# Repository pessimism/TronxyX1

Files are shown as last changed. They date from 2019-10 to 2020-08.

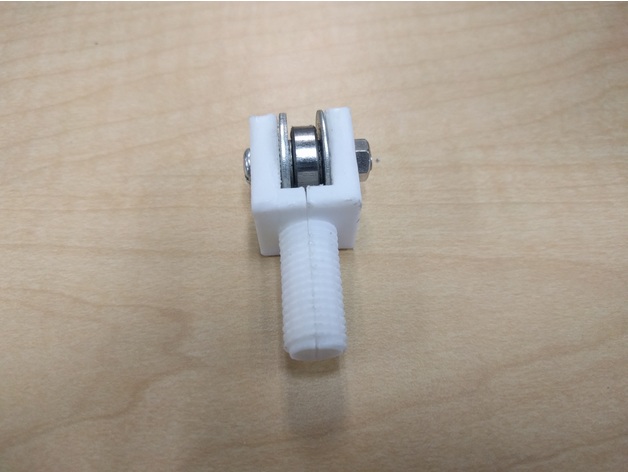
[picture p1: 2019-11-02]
Models/Parts/3d_printer_belt_tensioner/images/830ebf25c9036d7032c9400a6b96da95_preview_featured.jpg

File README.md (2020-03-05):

# TronxyX1

## Introduction

The [Tronxy X1](http://www.tronxy.com/x-series/tronxy-x1.html) is a budget cantilever design 3D printer by Tronxy.  I purchased this as my entry into the world of 3D printing.  

This repository contains documentation and resources I have collected while experimenting with this printer.

## Purchasing

All purchasing information here is focused on purchasing from Canada in Canadian Dollars (CAD).

I purchased my Tronxy X1 at [GearBest](https://www.gearbest.com/3d-printers-3d-printer-kits/pp_494192.html).  At the time of purchase, the kit was on flash sale for $133.  I was not given an option to choose shipping for this deal.  It was shipped by DHL and time from order to arrival was one week including a weekend.  There were some surprise customs fees from DHL bringing total cost to $159 to my door.  To their credit, DHL made payment of customs fees a painless online process and sent SMS status messages about the shipment and the need to pay fees.  

My first filament purchase was the [Sunlu PLA+](http://www.sunlugw.com/pd.jsp?id=52#_pp=151_1343) from [Amazon Canada](https://www.amazon.ca/gp/product/B07FXJ6PKQ/ref=ppx_yo_dt_b_asin_title_o04_s00?ie=UTF8&psc=1).  Cost for the 1KG spool was $20.39 on sale plus taxes totalling $23.04 (I have a Prime membership so did not pay extra for shipping).  The filament appears to be of good quality so far and I have not yet had any clogging or other issues caused by filament quality.

[CCTREE PLA](https://www.amazon.ca/CCTREE-1-75mm-PLA-Printer-Filament/dp/B07737W8Y9) So far seems to print at a lower temperature with fewer stringing/blobbing issues than the Sunlu.

I purchased this [ten pack of roller wheels](https://www.amazon.ca/gp/product/B07CWM3GCM/ref=ppx_yo_dt_b_asin_title_o03_s00?ie=UTF8&psc=1) at a shipped cost of $1.58 each to replace one wheel shipped with the unit that was scratched causing the x-axis to catch on the rail at a certain point.  The new wheel worked but these appear to be of poor quality, do not spin effortlessly by hand and have slight surface imperfections in the plastic.  I will search for higher quality rollers later as an upgrade option.

## Folder Structure

Documentation - The factory documentation shipped with the printer

Drivers - The USB to serial interface driver required to control the printer by computer

Models - Model files for the factory demo part, useful calibration items and upgrade parts specific to the printer

Profiles - Printer and Filament configuration profiles I have built and found to work well with my particular setup.

Marlin 2.0 Config - Configuration files to build Marlin 2.0 firmware for the printer

## Bed Adhesion

I had difficulty with adhesion with the bare Garolite build plate and Sunlu PLA+.  I added a layer of inexpensive 3M green painter's tape locally purchased and had much better results.

After printing and removing several items I had adhesion issues again which were improved by wiping down the tape surface with alcohol, finger oils can make the difference between adhesion and failure.

After more printing I've abandoned the tape for now and lightly sanded the Garolite with sandpaper, cleaned with alcohol and use a layer of cheap glue stick that I wash off and reapply every few prints.  I find this faster and simpler than dealing with the tape, which I have found in some instances can actually be lifted off the Garolite by a warping print.

## Firmware Calibration
I found that even after belt tensioning to the best of my ability with the provided hardware, I had to very slightly increase the X steps/mm to get true squares/circles.  I attribute this to differences in belt tension between axes

I found my extruder was underextruding and steps/mmm needed to be increased by almost 10%.  Never assume factory calibration is correct.  This can also change from one filament to the other.  I did the adjustment using [this guide](https://all3dp.com/2/extruder-calibration-6-easy-steps-2/)

## Extruder Issues
While trying to eliminate stringing and blobbing on prints I found that the bowden tube was not fully inserted into either coupler.  The end going into the hot end was also not cut flat, so I re-trimmed the end. Trimming and re-seating the tube noticeably improved print quality.

## Marlin 2.0
I opted to upgrade the printer to Marlin 2.0 from the stock Repetier 0.91 firmware.  This gave me thermal runaway protection, a serious omission from the printer.  I was also able to add several features from much more expensive units such as print pausing and resume from power failure.  This process requires several parts to be purchased as the stock Melzi board does not ship with a bootloader installed so it can't be flashed by USB.  The way I completed the process requires:

[An Arduino UNO or compatible board](https://www.amazon.ca/gp/product/B01MTMDT29/ref=ppx_yo_dt_b_asin_title_o04_s00?ie=UTF8&psc=1) ~$15

[Female to Female AND Female to Male Dupont Jumper Wires](https://www.amazon.ca/gp/product/B01EV70C78/ref=ppx_yo_dt_b_asin_title_o02_s00?ie=UTF8&psc=1) ~$12

A computer with the [Arduino IDE](https://www.arduino.cc/en/Main/Software) installed

A copy of the [Marlin 2.0 Source Code](http://marlinfw.org/meta/download/)

I will not detail all steps here as there are several good guides available online to outline the process.  I found [this one](https://www.instructables.com/id/Flashing-a-Bootloader-to-the-CR-10/) to be the most accurate.  In a nutshell you must

+ Program the UNO device via USB to act as a flashing tool 
+ Wire the UNO device to the Melzi board using six jumper wires
+ Flash a bootloader to the Melzi board via PC USB -> UNO -> Melzi connection
+ Disconnect UNO board
+ Build Marlin 2.0 using the correct Configuration.h file and any further adjustments to the Configuration_adv.h file
+ Flash Marlin to the Melzi board via PC USB

I had to make a few adjustments to the stock example Configuration and Configuration_adv files for the Tronxy X1:

+ The bed offsets were incorrect so prints were not centered in the print area
+ The thermal runaway protection was too aggressive for my room temperature and heater calibration and would error before heating was complete.  I relaxed the values as described in the documentation
+ I added my PID heater calibration values to replace the firmware defaults and made sure PID temperature control was enabled.  Further information [here](https://reprap.org/wiki/PID_Tuning)
+ I've noticed some inconsistencies in the keys required to activate menu items.  Some use left/right, some use up to confirm.  Have not resolved that yet, but all functions do work.

## Belt idler upgrade to tensioners
I purchased these [2020 extrusion compatible belt tensioners](https://www.aliexpress.com/item/4000056015276.html?spm=a2g0s.9042311.0.0.2c824c4djNLGq6) ~$15 to replace the stock single sided acrylic brackets and smoothg idler bearings.  This was the single largest upgrade in print quality I have done.  They are far better quality than the stock hardware, have toothed idlers to better fit the belt, and made a large improvement in the printer's ability to make accurate circles.  This was noticable right away in the stock demo pillar file included with the printer.  The drawback is a loss of 25mm of bed area due to the Y tensioner stopping the bed wheel from reaching the end of the extrusion.

## Part Cooling Fan
I printed [this](https://www.thingiverse.com/thing:2699842) and added a 5015 fan using spare mounting nuts and screws included with the printer.  There is an open fan header on the Melzi board for this purpose.  To get proper alignment I had to rotate the heat block slightly and tweak the fan mount/shroud a little.  I have found the fan helps to prevent distortion and stringing on small posts, but it also causes the base of parts to curl up off the bed, so it is only useful in specific circumstances.

## Fan Upgrades
I upgraded the hotend fan to [this](https://www.amazon.ca/gp/product/B009NQLT0M/ref=ppx_yo_dt_b_asin_title_o00_s00?ie=UTF8&psc=1) Noctua NF-A4x10 FLX fan for a huge decrease in operating noise.  The high pitched tone from the stock fan is completely gone and I have observed no cooling issues from the lower RPM fan

I am planning to upgrade the generic 5015 fan to [this](https://www.digikey.ca/product-detail/en/sunon-fans/MF50151VX-B00U-A99/259-1829-ND/7691033) Sunon MF50151VX-B00U-A99 fan in hopes to reduce operating noise further

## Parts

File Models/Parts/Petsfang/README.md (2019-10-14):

# Models

In this directory are a collection of models for testing, calibration and improvements for the printer.  Thank you to all of the great creators on thingiverse for sharing their work with the world.

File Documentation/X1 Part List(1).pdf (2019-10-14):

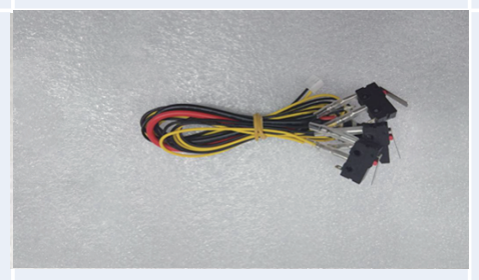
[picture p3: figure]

No. | Picture | Details | Quantity | Check | No. | Picture | Details | Quantity | Check
1-1 | | Limit switch | 3 | | 1-2 | | DC power jack | 1

# X1 Part List

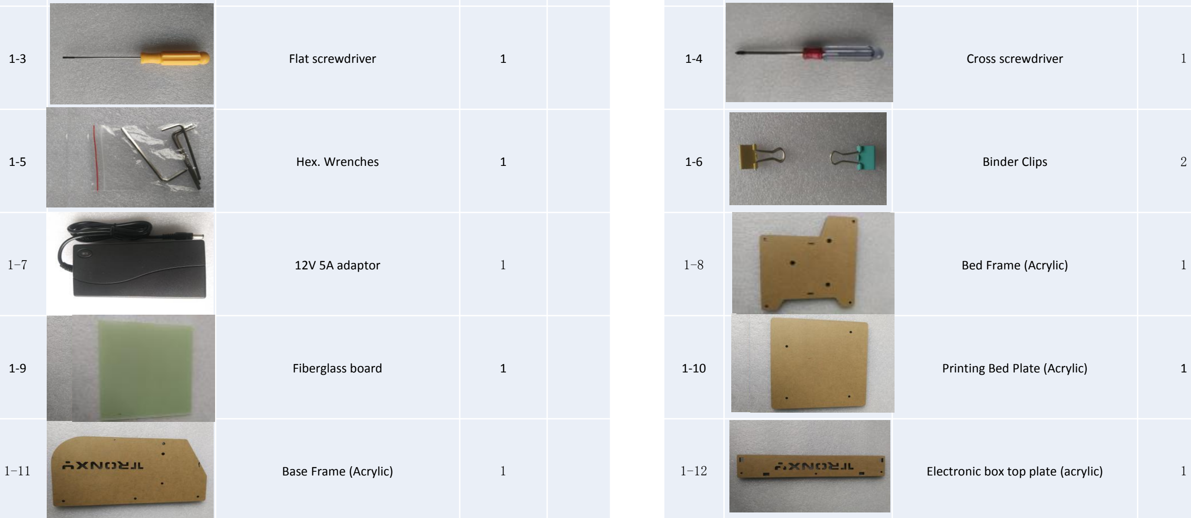
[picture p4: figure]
Flat screwdriver; Cross screwdriver; Hex. Wrenches; Binder Clips; 12V 5A adaptor; Bed Frame (Acrylic); Fiberglass board; Printing Bed Plate (Acrylic); Base Frame (Acrylic); Electronic box top plate (acrylic)
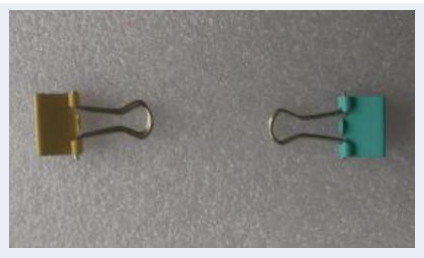
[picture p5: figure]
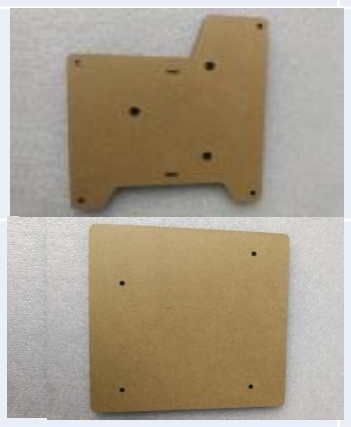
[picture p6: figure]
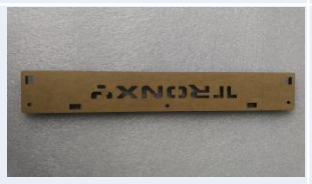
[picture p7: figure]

No. | Picture | Details | Quantity | Check | No. | Picture | Details | Quantity | Check
1-13 | | Electronic box Back plate (acrylic) | 1 | | 1-14 | | Electronic box bottom plate (acrylic) | 1
1-15 | | Electronic box front plate (acrylic) | 1 | | 1-16 | | LCD cable | 1

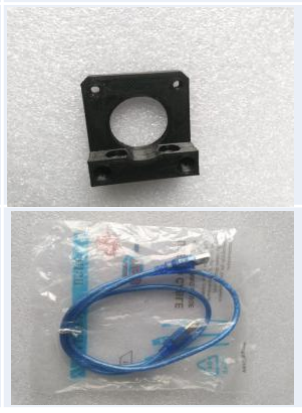
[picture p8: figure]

1-17 | | Electronic box side plate (acrylic) | 2 | | 1-18 | | Z-motor seat | 1
1-19 | | Card reader & Micaro SD card | 1 | | 1-20 | | USB cable | 1
1-21 | | X-motor mount (acrylic) | 1
2-1 | | Extruded bracket | 1 | | 2-2 | | Screws kits | 1
2-3 | | Motor wires | 4 | | 2-4 | | Small acrylic kits | 1

No. | Picture | Details | Quantity | Check | No. | Picture | Details | Quantity | Check

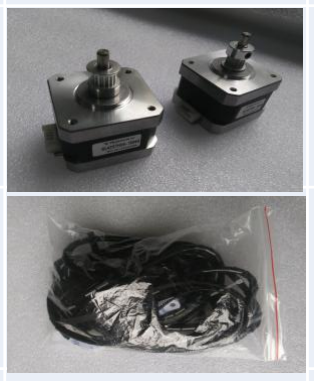
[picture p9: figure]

2-5 | | Z-axis motor (with coupling) | 1 | | 2-6 | | X-axis & Y-axis motors (With Pulley) | 2
2-7 | | Extruder (assembled) | 1 | | 2-8 | | Timing belt x 2pcs Winding pipe Cable ties | 1

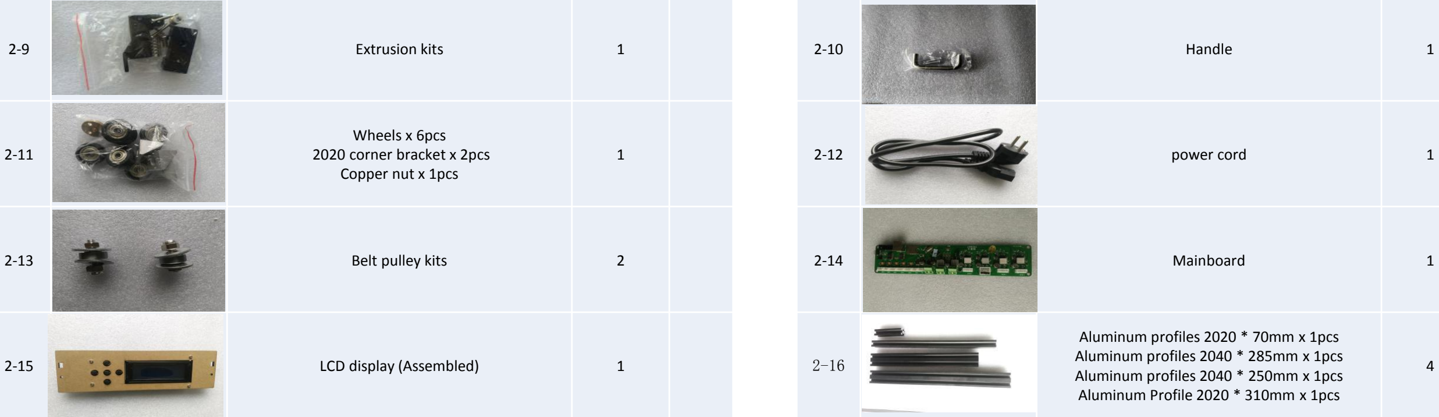
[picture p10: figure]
Extrusion kits; Handle; Belt pulley kits; Mainboard

2-11 | | Wheels x 6pcs 2020 corner bracket x 2pcs Copper nut x 1pcs | 1 | | 2-12 | | power cord | 1


2-15 | | LCD display (Assembled) | 1 | | 2-16 | | Aluminum profiles 2020 * 70mm x 1pcs Aluminum profiles 2040 * 285mm x 1pcs Aluminum profiles 2040 * 250mm x 1pcs Aluminum Profile 2020 * 310mm x 1pcs | 4
2-17 | | Threaded Rod | 1 | | 2-18 | | Extrusion motor(with gear) | 1

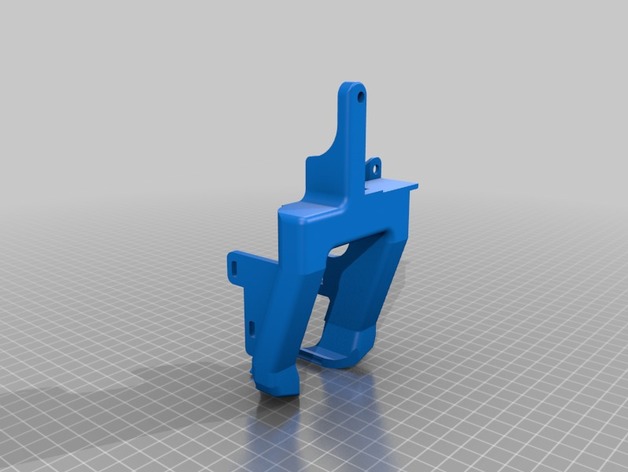
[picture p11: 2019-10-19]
Models/Parts/Petsfang/images/e7358cb4e06ece17424f1373e9a6f965_preview_featured.jpg

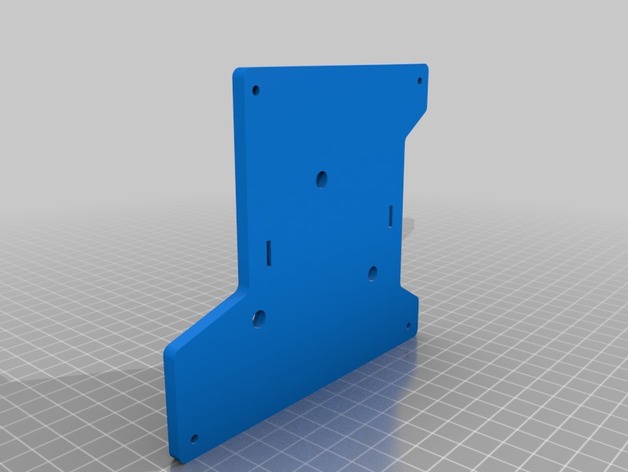
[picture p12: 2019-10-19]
Models/Parts/TronXY_X1_Brackets_Set/images/82e442813879a9bdd6b8e6a65d5bd545_preview_featured.jpg

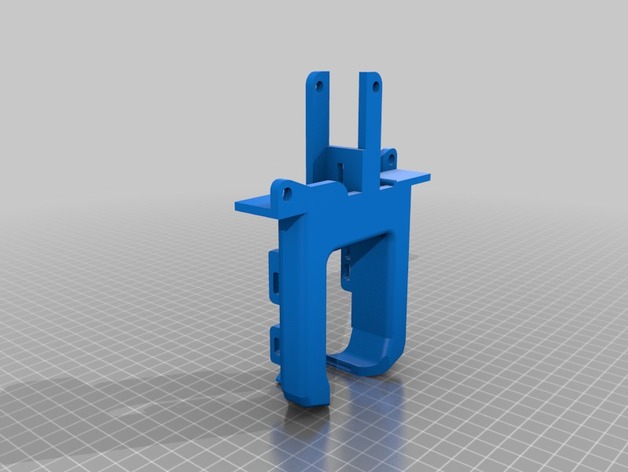
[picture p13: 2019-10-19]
Models/Parts/Petsfang/images/7c1312b0288502d47e82f708cd653ed2_preview_featured.jpg

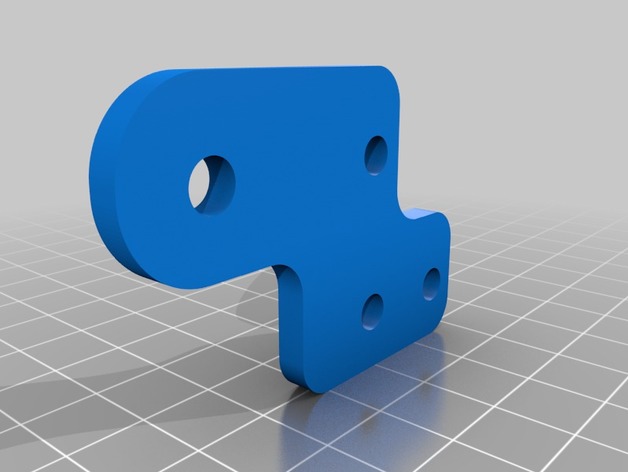
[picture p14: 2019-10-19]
Models/Parts/TronXY_X1_Brackets_Set/images/78606b93417cc2ece47546eed14306c8_preview_featured.jpg

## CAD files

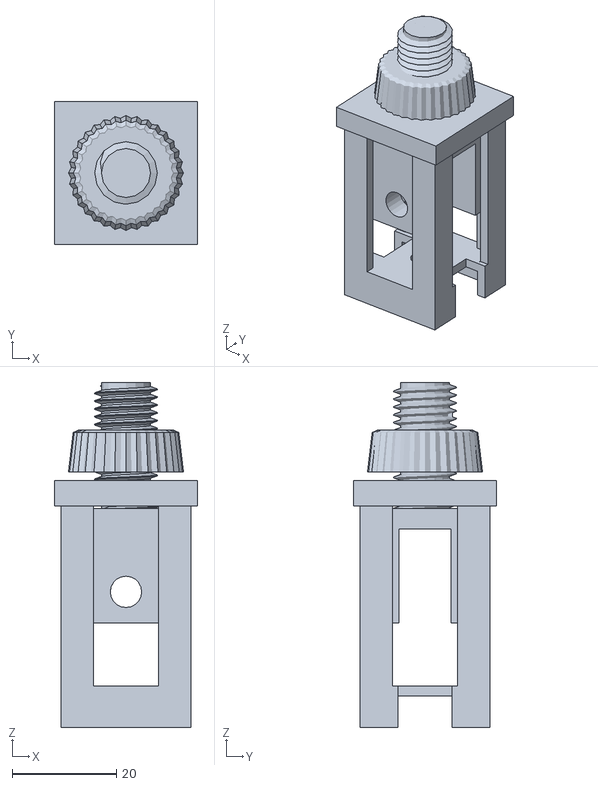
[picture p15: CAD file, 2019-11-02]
Models/Parts/3d_printer_belt_tensioner/files/Belt_tensioner_-_assembled.stl
27.5 x 27.5 x 66.1

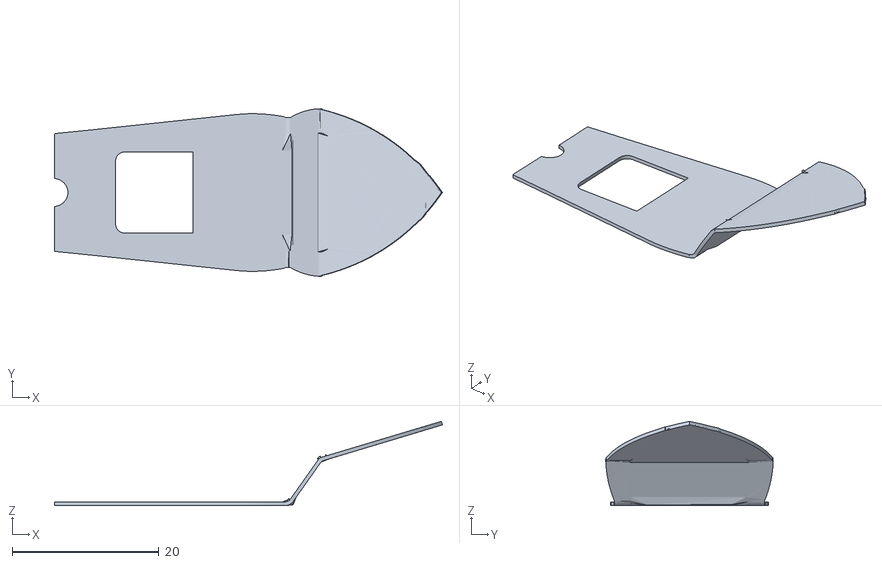
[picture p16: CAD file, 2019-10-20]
Models/Calibration/_3DBenchy_-_The_jolly_3D_printing_torture-test_by_CreativeTools.se/files/3DBenchy_-_Multi-part_-_Single_-_Deck_surface_-_3DBenchy.com.stl
52.9 x 22.8 x 11.5

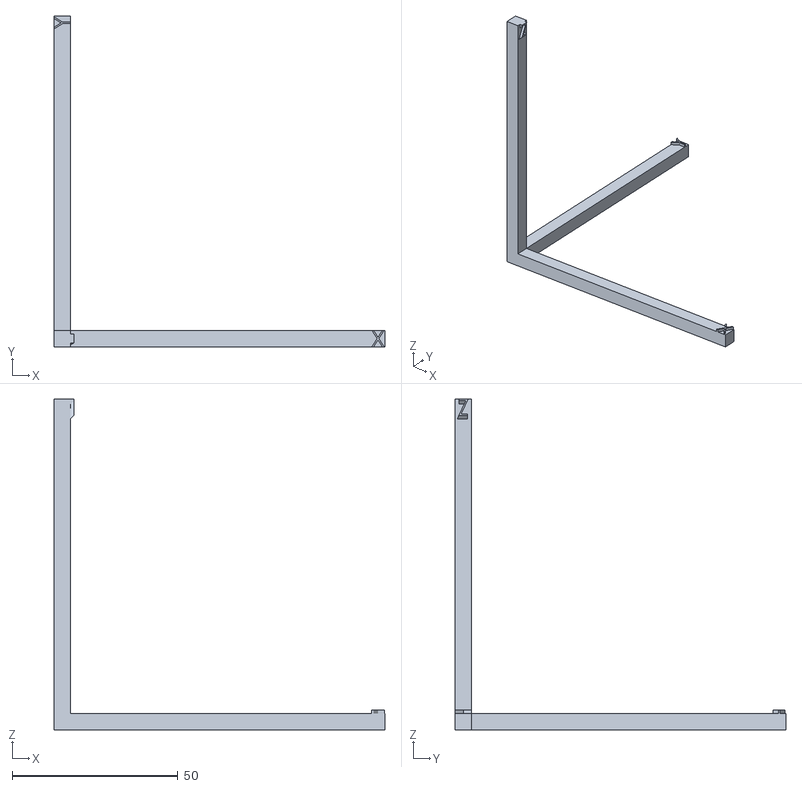
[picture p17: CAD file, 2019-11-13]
Models/Calibration/Calibration_Axes/calibration_axis.STL
100.0 x 100.0 x 100.0

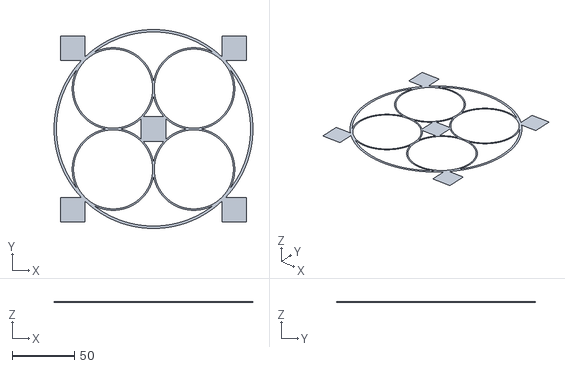
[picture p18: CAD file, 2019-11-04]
Models/Calibration/First_layer_calibration_/files/First_layer_calibration.stl
160.2 x 160.2 x 0.2

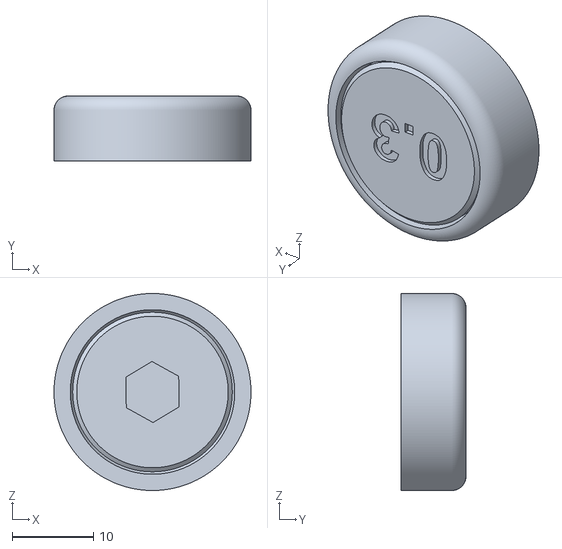
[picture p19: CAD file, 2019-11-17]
Models/Calibration/Individual_tolerance_tests/files/0.3.stl
24.2 x 8.00 x 24.2

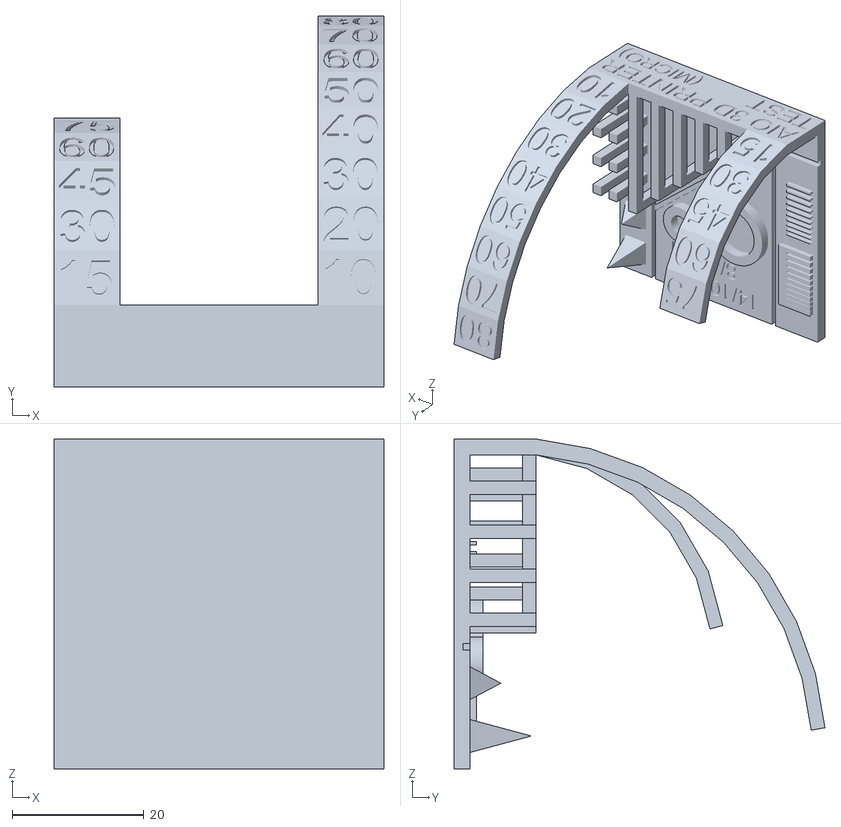
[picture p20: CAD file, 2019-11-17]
Models/Calibration/MICRO_All_In_One_3D_printer_test/files/AIl_In_One_3D_printer_test_micro.stl
50.0 x 56.2 x 50.0

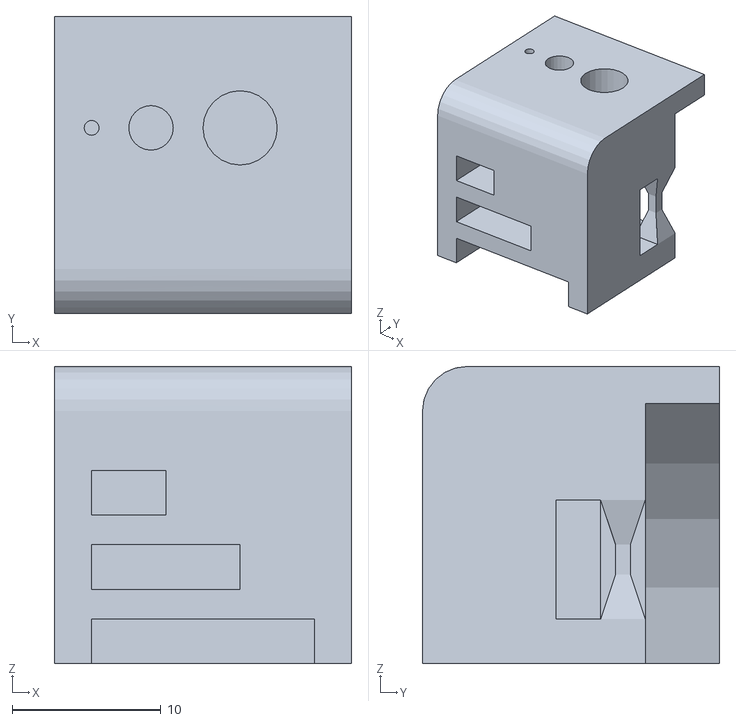
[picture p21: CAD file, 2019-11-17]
Models/Calibration/pockettest/files/Pocketest.stl
20.0 x 20.0 x 20.0

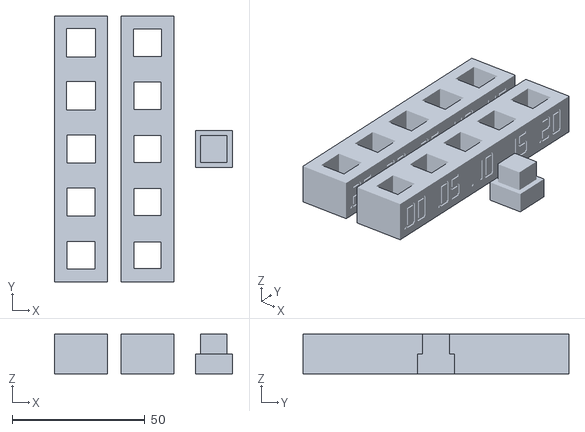
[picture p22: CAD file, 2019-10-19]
Models/Calibration/Snappy Reprap slop calibrator/slop_calibrator_parts.stl
67.0 x 100.0 x 15.0

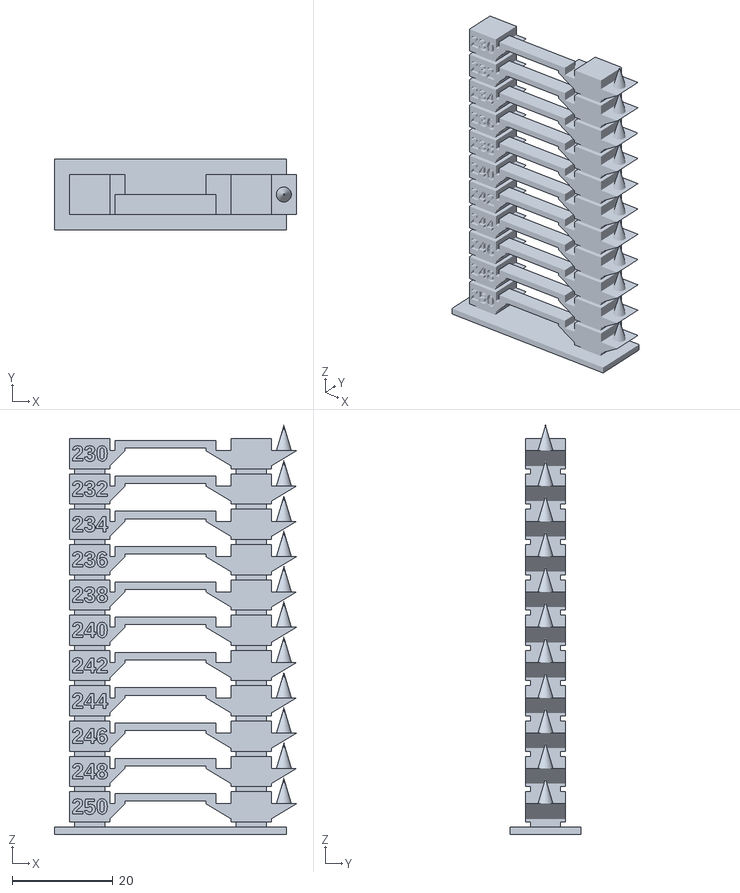
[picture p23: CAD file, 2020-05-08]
Models/Calibration/tempTower/tempTower.stl
48.0 x 14.0 x 81.1

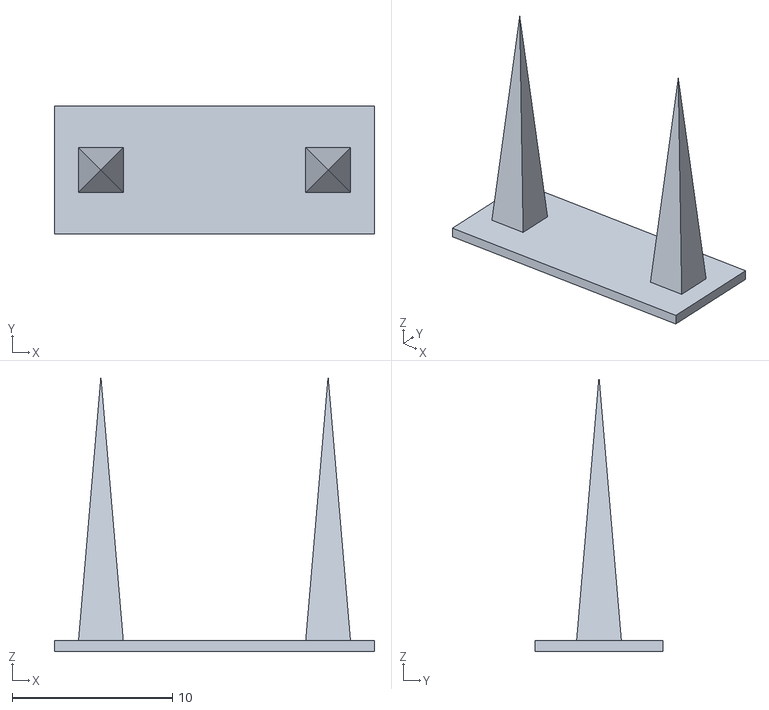
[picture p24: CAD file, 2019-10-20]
Models/Calibration/Ultrafast_and_economical_stringing_test/files/string_test_fast_pyramid.stl
20.0 x 8.00 x 17.2

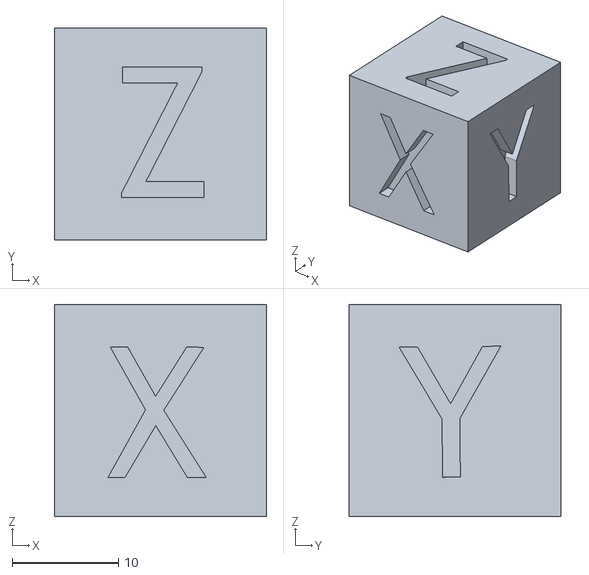
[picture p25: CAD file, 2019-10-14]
Models/Calibration/XYZ_20mm_Calibration_Cube/files/xyzCalibration_cube.stl
20.0 x 20.0 x 20.0

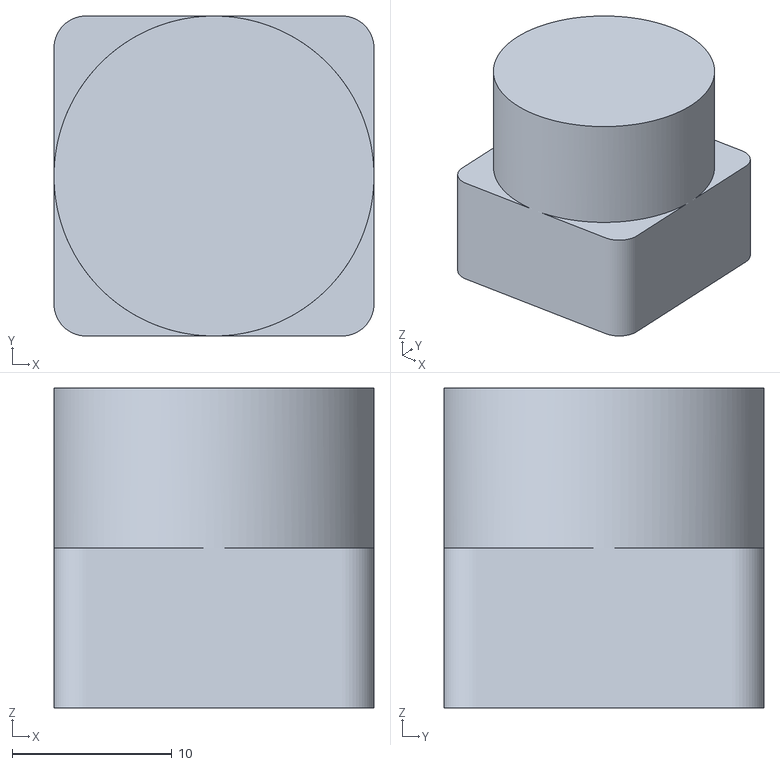
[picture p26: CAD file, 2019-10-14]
Models/Demo/20mm_box_pillar.stl
20.0 x 20.0 x 20.0

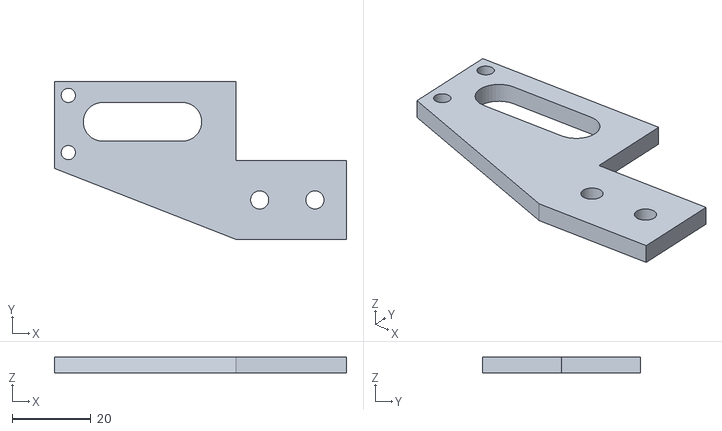
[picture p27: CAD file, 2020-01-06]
Models/Parts/bracket for tensioner/bracket.stl
74.0 x 40.0 x 4.00

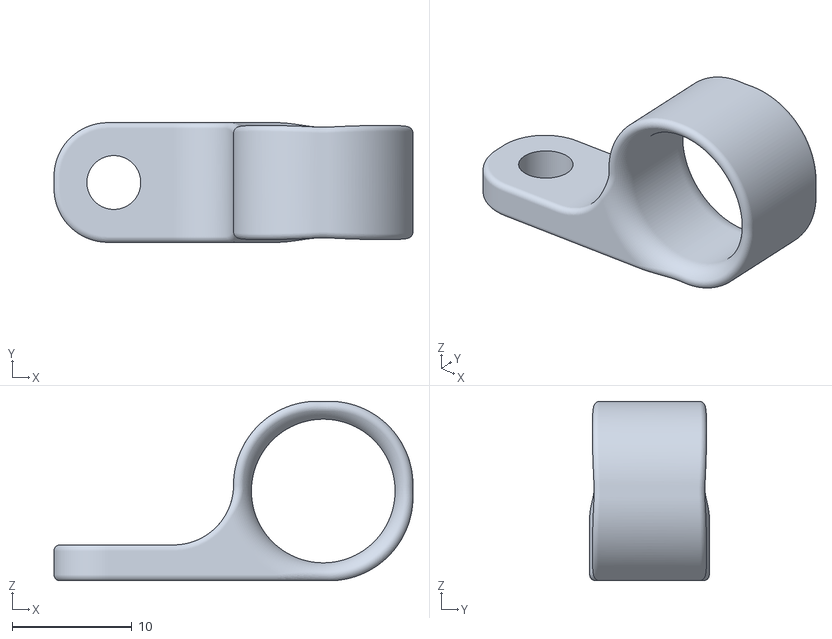
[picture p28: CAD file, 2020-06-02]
Models/Parts/Cable Guide/Cable Guide v4.stl
30.0 x 10.0 x 15.0

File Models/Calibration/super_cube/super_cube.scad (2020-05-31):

$fn=100;

difference(){
    cube([20,20,20]);
    translate([1,1,2])rotate([90,0,0])linear_extrude(height=1)text("Super",size=5);
    translate([19,1,12])rotate([90,0,90])linear_extrude(height=1)text("Cube",size=5);
    translate([10,1,19])rotate([0,0,90])linear_extrude(height=1)text("20x20x20",size=3);
    translate([0,9,0])rotate([0,90,0])cylinder(d=15,h=20);
    translate([14,1,12])rotate([90,0,0])linear_extrude(height=1)text("8mm",size=2);
    translate([10,0,15])rotate([-90,0,0])cylinder(d=8,h=20);
    translate([2,0,15])cube([3,20,5]);
    translate([0,3,15])cube([2,14,5]);
    translate([17,17,0])cube([3,3,20]);
}

difference(){
    translate([17,17,0])cylinder(d=6,h=20);
    translate([0,9,0])rotate([0,90,0])cylinder(d=15,h=20);
}

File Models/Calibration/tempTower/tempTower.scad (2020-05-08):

X=+0; Y=+1; Z=+2;

/* [General] */
// temperature of the first lowest block
start_temp = 250;
// temperature of the last highest block
end_temp = 230;
// change in temperature between successively printed blocks
temp_step = -2;


/* [Detail Geometry] */
// dimensions of the base plate
base = [46, 14, 1.5];
// dimensions of the pedestal under a tower block
pedestal = [6, 6, 1];
// dimensions of the tower block
block = [8, 8, 6];
// X spacing between the towers
tower_x_distance = 16*2;
// left (X-) overhang size
overhang_l_x = 3;
// right (X+) overhang size
overhang_r_x = 5;
// top of the overhang relative to the top of the block
overhang_z_top = -2.394;
// height of the overhang
overhang_z = 3;
// gap between the bridge and the left (X-) tower
bridge_l_gap = 1;
// gap between the bridge and the right (X+) tower
bridge_r_gap = 3;
bridge_y_front = -block[Y]/2;
bridge_y = block[Y]/2;
// top of the bridge relative to the top of the block
bridge_z_top = -0.394;
// thickness of the bridge
bridge_z = 1.5;
// embossing depth of the text
text_depth = 1;
// font used for the text
text_font = "Helvetica:style=Bold";
// text ascent relative to the width of the tower block
text_ascent = 0.4;


module Tower(x, overhang, gap, addpoint, label)
    translate([x,0,0])
    scale([x<=0 ? 1 : -1, 1, 1])
{
    z1 = 0;
    translate([0,0,z1 + pedestal[Z]/2]) cube(pedestal, true);
    z2 = z1 + pedestal[Z];
    label = label ? str(label) : "0";
    difference() 
    {
        translate([0,0,z2 + block[Z]/2]) cube(block, true);
        translate([0, -block[Y]/2+text_depth-0.001, z2 + block[Z]/2])
        rotate([90,0,0])
        linear_extrude(text_depth)   
        if (addpoint==0){
            text(label, size = block[X] * text_ascent, 
                 valign = "center", halign = "center",
                 font = text_font);
        }
    }
    
    overhang_pts = [[0,0],[0,-overhang_z],[overhang,0]];
    z3 = z2 + block[Z];
    z4 = z3 + overhang_z_top;
    translate([block[X]/2, block[Y]/2, z4])
        rotate([90,0,0])
        linear_extrude(block[Y])
        polygon(points=overhang_pts);
    
    // make overhang with pointy cone on right side:
    if (addpoint==1)
    {   // overhang
        translate([-block[X]/2, -block[Y]/2, z4])
            rotate([90,0,180])
            linear_extrude(block[Y])
            polygon(points=overhang_pts);
        // pointy cone
        translate([-block[X]/2-overhang/2, 0, z4])
            cylinder($fn = 20, h=block[Z]-1, r1=1.5, r2=0, center=false);  
    }
    
    pedestal_z = abs(overhang_z_top -bridge_z_top + bridge_z);
    translate([block[X]/2 + gap, bridge_y_front, z4]) 
    {
        cube([(overhang-gap)-0.01, bridge_y-0.01, pedestal_z]);
        translate([0,0,pedestal_z])
            cube([abs(x)-block[X]/2-gap, bridge_y, bridge_z]);
    }
}

z1 = 0;
translate([0,0,z1+base[Z]/2]) cube(base, true);
z2 = z1 + base[Z];

count = (end_temp - start_temp)/temp_step;

echo("start_temp=", start_temp);
echo("end_temp=", end_temp);
echo("temp_step=", temp_step);
echo("count=", count);

for (i = [0 : abs(count)]) 
{
    z3 = z2 + i*(pedestal[Z] + block[Z]);
    temp = start_temp + i*abs(temp_step);
    echo("-> ", i, ": temp=", temp);

    translate([0,0,z3]) 
    {
        if(start_temp < end_temp) 
            { Tower(-tower_x_distance/2, overhang_l_x, bridge_l_gap, 0, (start_temp + i*abs(temp_step))); }
        else
            { Tower(-tower_x_distance/2, overhang_l_x, bridge_l_gap, 0, (start_temp + -i*abs(temp_step))); }

        Tower(tower_x_distance/2, overhang_r_x, bridge_r_gap, 1);
    }
}

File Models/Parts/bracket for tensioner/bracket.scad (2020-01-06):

//To replace one side of this tensioner https://www.aliexpress.com/item/4000056015276.html
//and make it more like this one https://www.aliexpress.com/item/32993306070.html
//so that the Y carriage roller can travel the full length of the extrusion without hitting the bracket

//All dimensions in MM

//Fudge factor for hole sizes to accomodate printer/filament tolerance
fudge = 0.6;

//Dimensions for bracket
length = 74;
height = 40;
thickness = 4;

//Dimensions for notch to allow v-wheel to clear
nlength = 28; 
nheight = 20;

//Pulley slot dimensions
pheight     = 9.2 + fudge;
prad        = pheight/2;
pfromleft   = 7.3;
pfromtop    = 5.3;
pslotlength = 27.5;

//Tensioner screw holes (M3)
tensioner_screw_hole_diameter              = 3 + fudge;
tensioner_screw_hole_center_dist_from_edge = 3.5;
tensioner_screw_hole_center_dist_from_mid = 2;

//T-Nut screw holes (M4)
tnut_screw_hole_diameter     = 4 + fudge;
right_tnut_offset_from_right = 8;
left_tnut_offset_from_right  = 22;

//Facet constant for hole roundness
facets = 40;

//Constant for 10mm centering of T-Nut screw holes for 2020 extrusion
2020_tnut_height = 10;

//Thanks to https://github.com/openscad/MCAD/blob/master/triangles.scad
module triangle(o_len, a_len, depth, center=false)
{
    centroid = center ? [-a_len/3, -o_len/3, -depth/2] : [0, 0, 0];
    translate(centroid) linear_extrude(height=depth)
    {
        polygon(points=[[0,0],[a_len,0],[0,o_len]], paths=[[0,1,2]]);
    }
}

//The bracket with the notch subtracted from it
difference()
{
    //Main bracket shape
    cube([length,height,thickness], center = false);
    
    //Move notch to correct place
    translate([(length-nlength),(height-nheight),0]){
        //Notch shape
        cube([nlength,nheight,thickness], center = false);
    }
    
    //Move left pulley hole to correct place
    translate([(prad + pfromleft),(height-pfromtop-prad),0]){
        //left pulley hole
        cylinder(h = thickness, d = pheight , center = false, $fn=facets);
    }
    
    //Move right pulley hole to correct place
    translate([(prad + pslotlength),(height-pfromtop-prad),0]){
        //right pulley hole
        cylinder(h = thickness, d = pheight , center = false, $fn=facets);
    }
    
    //Move pulley rectangle to correct place
    translate([(prad + pfromleft),(height-pfromtop-pheight),0]){
        //pulley rectangle between pulley holes
        cube([(pslotlength-pheight+pfromleft-prad),pheight,thickness], center = false);
    }
    
    //Move upper tensioner screw hole to correct place
    translate([(tensioner_screw_hole_center_dist_from_edge),(height-tensioner_screw_hole_center_dist_from_edge),0]){
        //upper tensioner screw hole
        cylinder(h = thickness, d = tensioner_screw_hole_diameter , center = false, $fn=facets);
    }
    
    //Move lower tensioner screw hole to correct place
    translate([(tensioner_screw_hole_center_dist_from_edge),(height/2 + tensioner_screw_hole_center_dist_from_mid),0]){
        //lower tensioner screw hole
        cylinder(h = thickness, d = tensioner_screw_hole_diameter , center = false, $fn=facets);
    }
    
    //Move right tnut screw hole to correct place
    translate([(length - right_tnut_offset_from_right),2020_tnut_height,0]){
        //right tnut screw hole
        cylinder(h = thickness, d = tnut_screw_hole_diameter , center = false, $fn=facets);
    }
    
    //Move left tnut screw hole to correct place
    translate([(length - left_tnut_offset_from_right),2020_tnut_height,0]){
        //left tnut screw hole
        cylinder(h = thickness, d = tnut_screw_hole_diameter , center = false, $fn=facets);
    }    
    
    triangle(18,length-nlength,4);
}

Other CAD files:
Models/Calibration/super_cube/super_cube.stl
Models/Parts/Cooling Ring/Cooling Ring v29.stl
Models/Parts/cooling set/Semi-Circular_Anet_A8_Fan_Duct/files/Semi-Circular_Anet_A8_Fan_Duct.stl
Models/Parts/cooling set/TronXY_X1_Radial_Fan_Mounting_Bracket/files/Fan_Bracket_new.STL
Models/Parts/Customizable_Spool_Hub_Adapter/spool_adapter_V1.4.scad
Models/Calibration/Individual_tolerance_tests/files/0.1.stl
Models/Calibration/Individual_tolerance_tests/files/0.15.stl
Models/Calibration/Individual_tolerance_tests/files/0.2.stl
Models/Calibration/Individual_tolerance_tests/files/0.25.stl
Models/Calibration/Individual_tolerance_tests/files/0.35.stl
Models/Calibration/Individual_tolerance_tests/files/0.4.stl
Models/Calibration/Individual_tolerance_tests/files/0.45.stl
Models/Calibration/_3DBenchy_-_The_jolly_3D_printing_torture-test_by_CreativeTools.se/files/3DBenchy.3mf
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

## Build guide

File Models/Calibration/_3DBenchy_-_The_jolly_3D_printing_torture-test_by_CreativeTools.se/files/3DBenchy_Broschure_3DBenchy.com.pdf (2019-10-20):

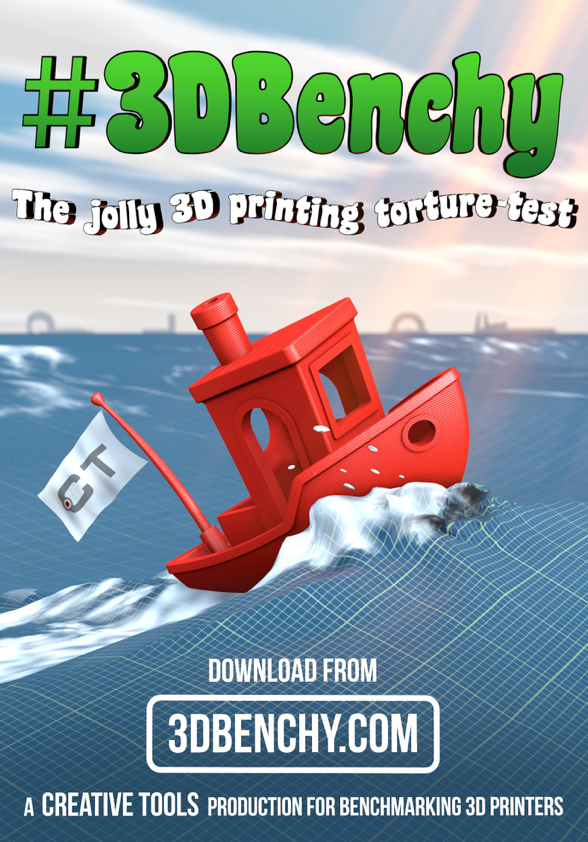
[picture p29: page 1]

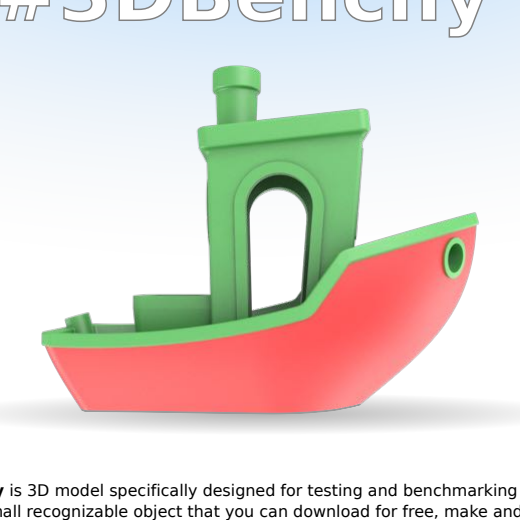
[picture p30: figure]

Download the #3DBenchy
high-res STL file from
3DBenchy.com/download
and import it into your
printer's software.

#3DBenchy is 3D model specifically designed for testing and benchmarking 3D printers. It is a small recognizable object that you can download for free, make and share.

#3DBenchy is designed by Creative-Tools.com as a calibration and torture-test part for 3D printers. To download the STL-file and read more about 3D printing please visit 3DBenchy.com.

# Share

#3DBenchy is released under a Creative Commons license (CC BY-ND 4.0). 3DBenchy.com/license

Download | 3D-print | Analyse | Follow
| Make #3DBenchy with your 3D printer. Try out different resolutions, software settings and materials. | Measure and analyse your #3DBenchy. Compare your print with the reference dimensions and other users' results.

Share your results! Simply tag your images and
videos on social media
with #3DBenchy. Visit
3DBenchy.com/share for
more information.
| | | See what others are printing and search for #3DBenchy on social media. Visit 3DBenchy.com/follow for more information.

# #3DBenchy

Visit www.3DBenchy.com to learn all about 3D printing technologies through tutorials, videos and get free profiles for different 3D printers..

# Learn more about 3D printing

# Features

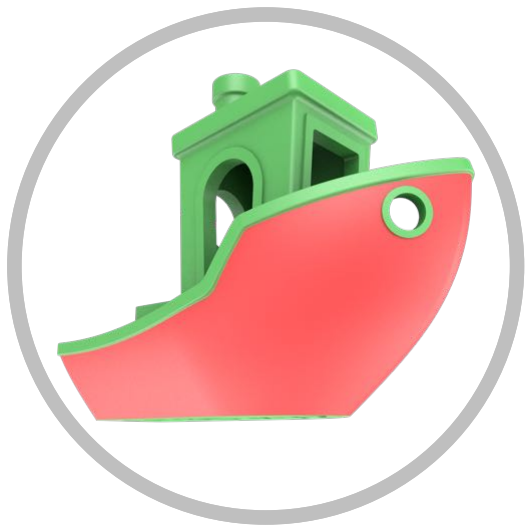
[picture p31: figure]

The hull is a large, smooth overhanging curved surface that is challenging to 3D-print and clearly reveals any
surface deviations.

# #3DBenchy is designed to offer a large array of challenging geometrical features for 3D

printers, and touch on different issues related to additive manufacturing.

The 3D model is designed to print at 1:1 scale without support materials. It is challenging

# for most 3D printers but the small volume (15.55 cm³) typically prints in well under two

hours and does not require much material.

Read all about #3DBenchy's features at www.3DBenchy.com.

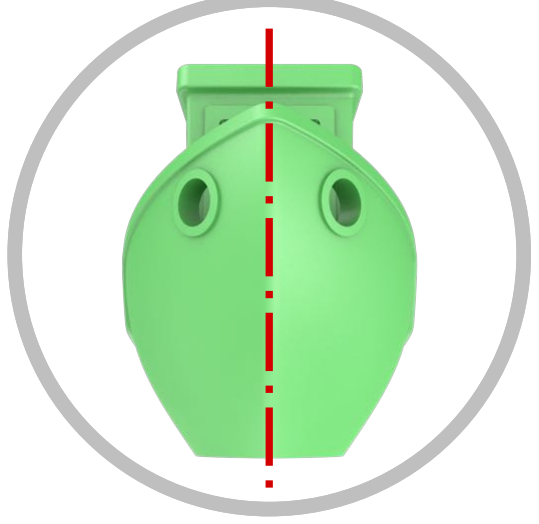
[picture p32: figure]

#3DBenchy is perfectly

symmetrical which makes
any skewness and warping
easy to detect.

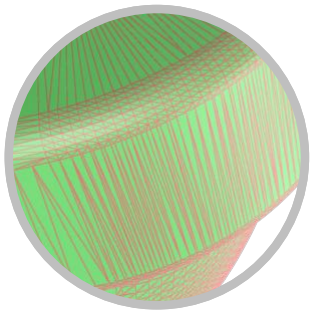
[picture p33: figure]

The STL file is triangulated at a very high resolution which yields smooth surfaces. The maximum deviation from the original CAD file is set to 0.001 mm.

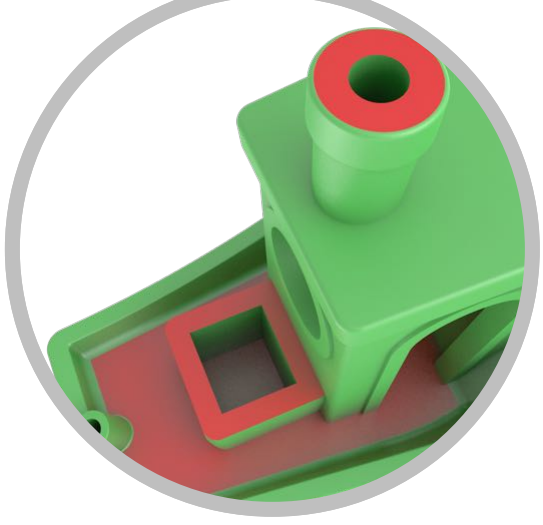
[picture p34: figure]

The top surfaces of the deck, box and chimney are planar, horizontal and parallel to the bottom plane.

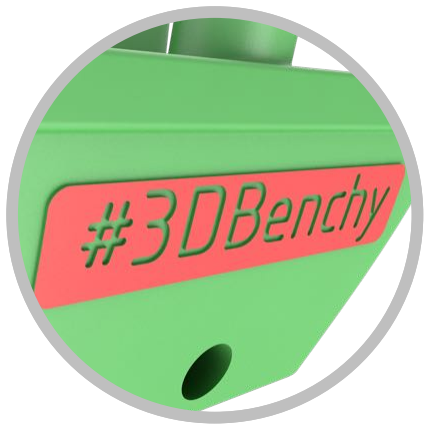
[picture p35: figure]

If you have a high-resolution 3D printer, this is where you can shine! The letters on the stern are less than 2 mm tall and the thickness of #3DBenchy's
nameplate is just 0.1 mm.

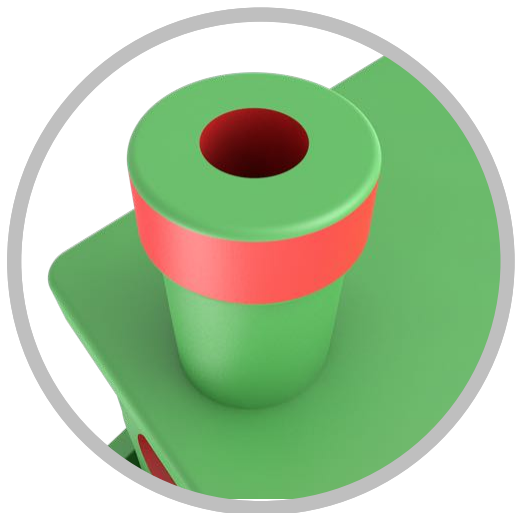
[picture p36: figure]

The chimney is designed to define concentrical cylindrical shapes with inner and outer diameters. These clearly show deviations in roundness.

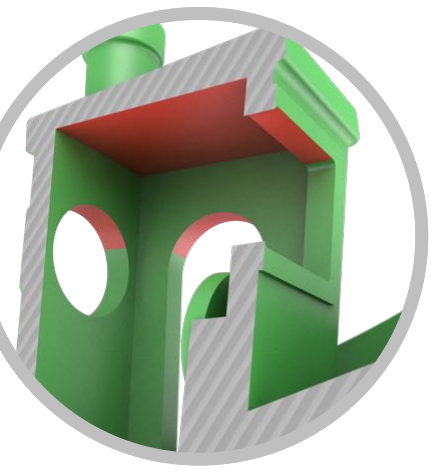
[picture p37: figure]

Overhang issues are the
Achilles' heel of 3D printing. #3DBenchy offers several
challenging areas such as in the difficult-to-reach inside of the bridge.

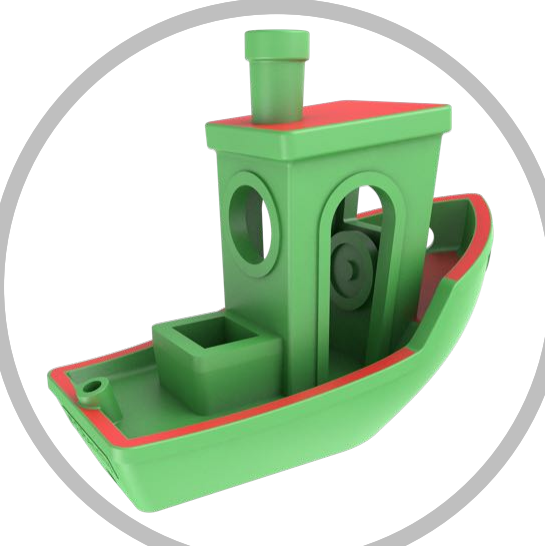
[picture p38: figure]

Low-slope-surfaces clearly show the layered structure of 3D printing. If printed
horizontally, #3DBenchy's
gunwale and roof of the bridge will reveal the layer-steps.

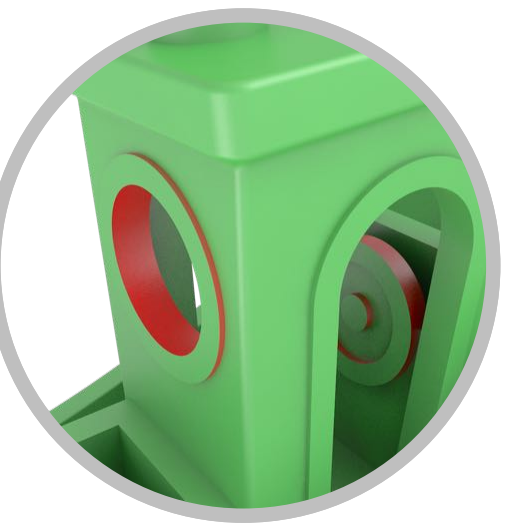
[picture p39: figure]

The rear window offers a large circular horizontal hole and the boat's wheel offers a round difficult-to-reach secluded feature.

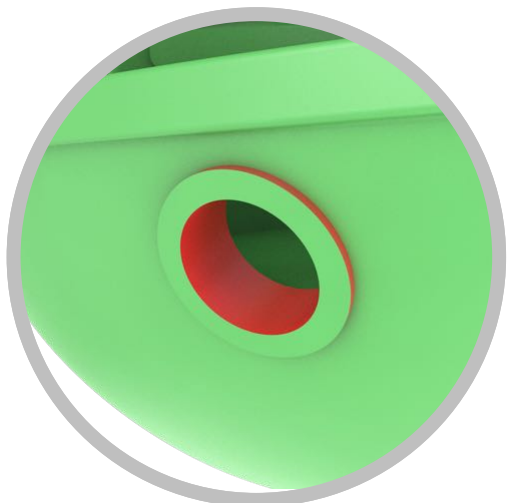
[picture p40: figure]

The hawsepipe represents a small short horizontal hole and has a very thin flange against the hull.

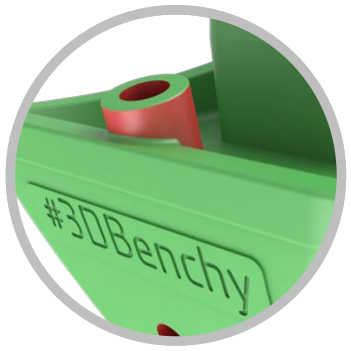
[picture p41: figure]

The fishing-rod-holder provides a very small slightly-slanted blind hole.

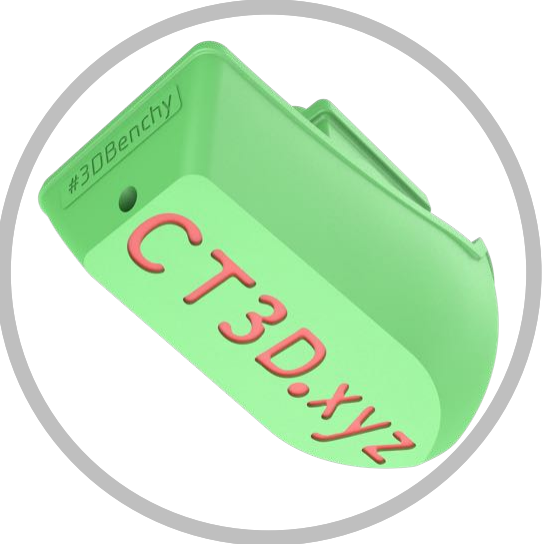
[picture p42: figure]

The shallow letters at the bottom of the boat clearly reveal typical first-layer-squashing.

To download the 3D model and read more about 3D printing please visit 3DBenchy.com.

# Measure and calibrate

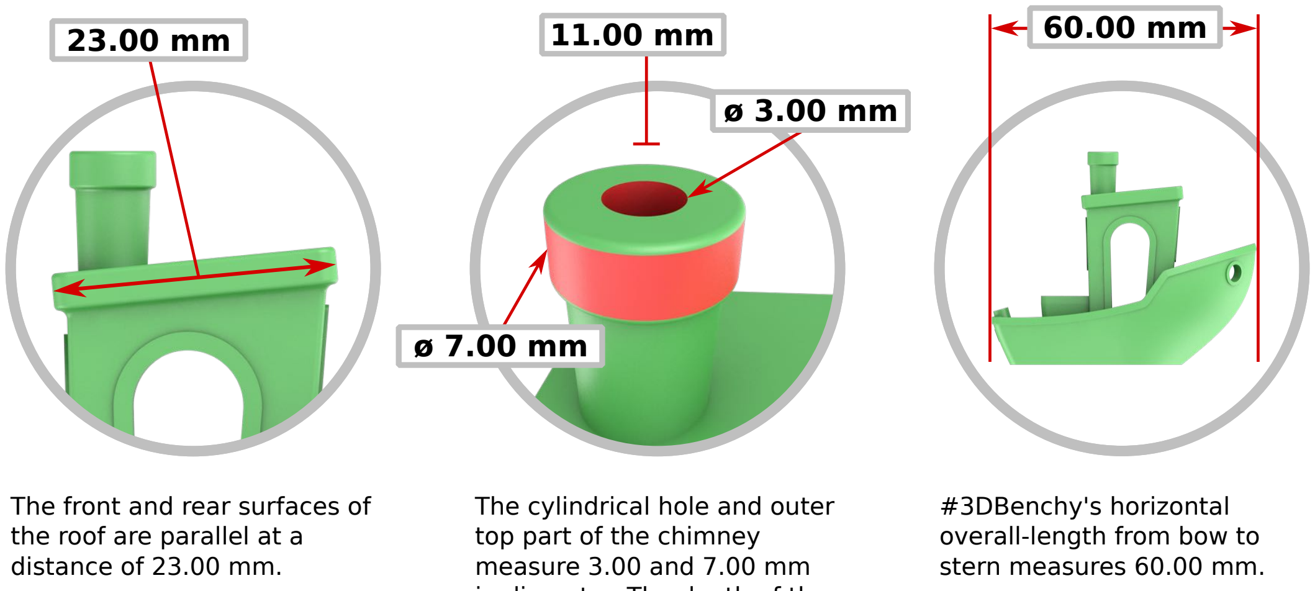
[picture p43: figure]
The front and rear surfaces of; distance of 23.00 mm.; The cylindrical hole and outer top part of the chimney measure 3.00 and 7.00 mm; #3DBenchy's horizontal overall-length from bow to stern measures 60.00 mm.
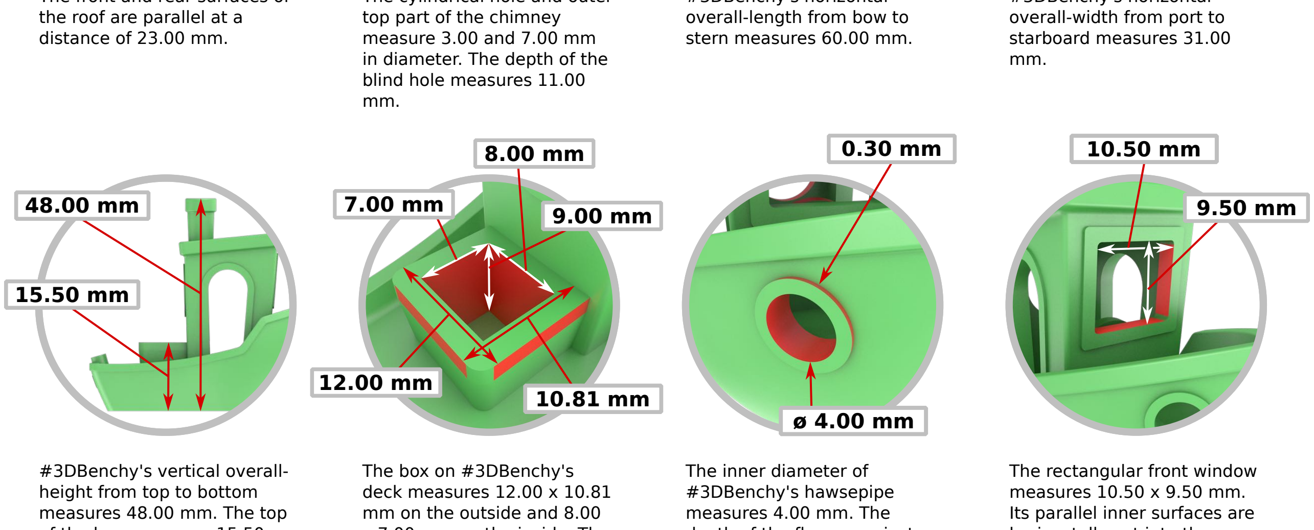
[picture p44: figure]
in diameter. The depth of the blind hole measures 11.00 mm.; overall-width from port to starboard measures 31.00 mm.; #3DBenchy's vertical overall- height from top to bottom measures 48.00 mm. The top; The box on #3DBenchy's deck measures 12.00 x 10.81 mm on the outside and 8.00; The inner diameter of #3DBenchy's hawsepipe measures 4.00 mm. The; The rectangular front window measures 10.50 x 9.50 mm. Its parallel inner surfaces are

the roof are parallel at a

# Use #3DBenchy to test and calibrate your 3D printer by adjusting hardware and

software settings for optimal results.

# The shape and size of this 3D model is designed to challenge 3D printers. Compare your #3DBenchy results with the dimensions illustrated below. These are easy to measure

with a caliper.

# Print and check your 3D-printer's result for dimensional accuracy, tolerances, warping

and deviations related to changes in printing parameters and material types.

#3DBenchy's horizontal

60.00 mm | 31.00 mm

horizontally cut into the
bridge.

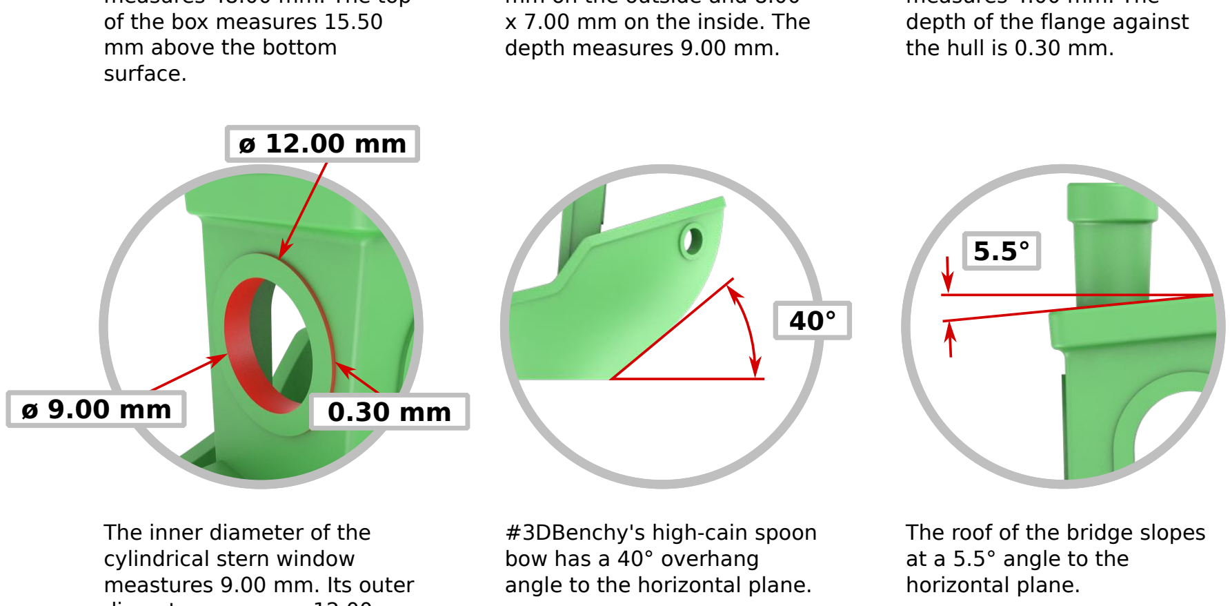
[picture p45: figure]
of the box measures 15.50 mm above the bottom surface.; x 7.00 mm on the inside. The depth measures 9.00 mm.; depth of the flange against the hull is 0.30 mm.; The inner diameter of the cylindrical stern window meastures 9.00 mm. Its outer; #3DBenchy's high-cain spoon bow has a 40° overhang angle to the horizontal plane.; The roof of the bridge slopes at a 5.5° angle to the horizontal plane.

diameter measures 12.00
mm. The flange's depth is
0.30 mm.

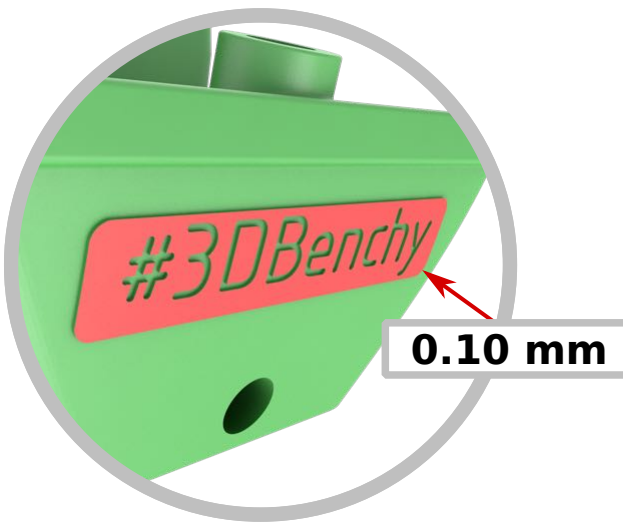
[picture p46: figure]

The sign and small letters at the stern are extruded at
0.10 mm.

To download the 3D model and read more about 3D printing please visit 3DBenchy.com.

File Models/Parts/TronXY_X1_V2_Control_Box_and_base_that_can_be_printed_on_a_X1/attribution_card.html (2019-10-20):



# TronXY X1 V2 Control Box and base that can be printed on a X1 by Adverse_Effects

## Published on March 4, 2018

### www.thingiverse.com/thing:2813891

####   

#### Creative Commons - Attribution - Non-Commercial

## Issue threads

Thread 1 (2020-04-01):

Marlin Firmware - #error "LEVEL_CORNERS_INSET is now LEVEL_CORNERS_INSET_LFRB . Please update your Configuration.h

aidanaedy, 2020-04-01:
I have tried to compile several versions of the marlin Tronxy X1 firmware whilst adding in your configuration.h and the configuration_adv.h files, but I get errors that it cannot compile as it is an out of date file. what versions does it work with.

Sorry, I cannot find an email address for you. My email is aidanaedy@gmail.com

Regards,
Aidan Aedy

pessimism, 2020-04-02:
Hello, the last version I tested the config with was Marlin 2.0.1.  If you use my config you will need to change the extruder steps/mm in configuration.h line 721 for the stock extruder back to 100, mine is changed because I replaced the extruder on my X1 with a different model

Closed 2020-04-02.

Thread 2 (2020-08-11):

Y-Axis Specific Tensioner

phineasthecat, 2020-08-11:
The tensioner you linked for the X and Y axes is meant just for the X-axis. There's a design for the Y-axis with the same step down as the stock acrylic fixed idler that's meant for Creality and Ender printers, but fits the TronXY cantilever printers too thanks to the identical belt routing design and use of 2040 profile for the Y-axis rail.

Example link on AliExpress (this listing sells both X and Y axes tensioners):
https://www.aliexpress.com/item/33049736568.html

The linked tensioner doesn't have a toothed pulley, but imo that's unnecessary (and just adds friction). The main problem with the stock idler setup is the low quality bearing, and only being affixed on one side. Ball bearings don't like shear forces, especially cheap ones.

Beyond the tensioner/idler design, there's also other sources of belt tension problems. The stock belts are pretty low quality, and varied in tension along their length on my printer; I ended up just buying better belts to completely solve the belt tension issue. I also had to swap both stock GT2-16 stepper pulleys for better ones, since they had noticeable (to my eye!) runout.

Thanks for the Marlin profile, btw!

pessimism, 2020-08-16:
You're right, I didn't realize until months later doing a large edge to edge print and smacking into the tensioner.  I ended up modelling and printing this guy https://github.com/pessimism/TronxyX1/blob/master/Models/Parts/bracket%20for%20tensioner/bracket.stl for one side of the Y tensioner.  I still lose a few MM of build area and need to remodel both sides of it for full clearance.

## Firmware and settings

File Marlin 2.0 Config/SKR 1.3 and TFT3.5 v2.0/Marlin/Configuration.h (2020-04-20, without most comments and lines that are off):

#pragma once
#define CONFIGURATION_H_VERSION 020005
#define STRING_CONFIG_H_AUTHOR "(Steve Trotman, 0.3)" // Who made the changes.
#define SHOW_BOOTSCREEN
#define SERIAL_PORT -1
#define SERIAL_PORT_2 0
#define BAUDRATE 115200
  #define MOTHERBOARD BOARD_BTT_SKR_V1_3
#define CUSTOM_MACHINE_NAME "Tronxy X1 SKR1.3"
#define EXTRUDERS 1
#define DEFAULT_NOMINAL_FILAMENT_DIA 1.75
#define TEMP_SENSOR_0 5
#define TEMP_SENSOR_1 0
#define TEMP_SENSOR_2 0
#define TEMP_SENSOR_3 0
#define TEMP_SENSOR_4 0
#define TEMP_SENSOR_5 0
#define TEMP_SENSOR_6 0
#define TEMP_SENSOR_7 0
#define TEMP_SENSOR_BED 0
#define TEMP_SENSOR_PROBE 0
#define TEMP_SENSOR_CHAMBER 0
#define DUMMY_THERMISTOR_998_VALUE 25
#define DUMMY_THERMISTOR_999_VALUE 100
#define MAX_REDUNDANT_TEMP_SENSOR_DIFF 10
#define TEMP_RESIDENCY_TIME     10  // (seconds) Time to wait for hotend to "settle" in M109
#define TEMP_WINDOW              1  // (°C) Temperature proximity for the "temperature reached" timer
#define TEMP_HYSTERESIS          3  // (°C) Temperature proximity considered "close enough" to the target
#define TEMP_BED_RESIDENCY_TIME 10  // (seconds) Time to wait for bed to "settle" in M190
#define TEMP_BED_WINDOW          1  // (°C) Temperature proximity for the "temperature reached" timer
#define TEMP_BED_HYSTERESIS      3  // (°C) Temperature proximity considered "close enough" to the target
#define HEATER_0_MINTEMP   5
#define HEATER_1_MINTEMP   5
#define HEATER_2_MINTEMP   5
#define HEATER_3_MINTEMP   5
#define HEATER_4_MINTEMP   5
#define HEATER_5_MINTEMP   5
#define HEATER_6_MINTEMP   5
#define HEATER_7_MINTEMP   5
#define BED_MINTEMP        5
#define HEATER_0_MAXTEMP 300
#define HEATER_1_MAXTEMP 275
#define HEATER_2_MAXTEMP 275
#define HEATER_3_MAXTEMP 275
#define HEATER_4_MAXTEMP 275
#define HEATER_5_MAXTEMP 275
#define HEATER_6_MAXTEMP 275
#define HEATER_7_MAXTEMP 275
#define BED_MAXTEMP      150
#define PIDTEMP
#define BANG_MAX 255     // Limits current to nozzle while in bang-bang mode; 255=full current
#define PID_MAX BANG_MAX // Limits current to nozzle while PID is active (see PID_FUNCTIONAL_RANGE below); 255=full current
#define PID_K1 0.95      // Smoothing factor within any PID loop
  #define PID_FUNCTIONAL_RANGE 10 // If the temperature difference between the target temperature and the actual temperature
#define DEFAULT_Kp 13.41
#define DEFAULT_Ki 0.71
#define DEFAULT_Kd 63.70
#define MAX_BED_POWER 255 // limits duty cycle to bed; 255=full current
#define PREVENT_COLD_EXTRUSION
#define EXTRUDE_MINTEMP 180
#define PREVENT_LENGTHY_EXTRUDE
#define EXTRUDE_MAXLENGTH 200
#define THERMAL_PROTECTION_HOTENDS // Enable thermal protection for all extruders
#define THERMAL_PROTECTION_BED     // Enable thermal protection for the heated bed
#define THERMAL_PROTECTION_CHAMBER // Enable thermal protection for the heated chamber
#define USE_XMIN_PLUG
#define USE_YMIN_PLUG
#define USE_ZMIN_PLUG
#define ENDSTOPPULLUPS
#define X_MIN_ENDSTOP_INVERTING true  // Set to true to invert the logic of the endstop.
#define Y_MIN_ENDSTOP_INVERTING true  // Set to true to invert the logic of the endstop.
#define Z_MIN_ENDSTOP_INVERTING true  // Set to true to invert the logic of the endstop.
#define X_MAX_ENDSTOP_INVERTING false // Set to true to invert the logic of the endstop.
#define Y_MAX_ENDSTOP_INVERTING false // Set to true to invert the logic of the endstop.
#define Z_MAX_ENDSTOP_INVERTING false // Set to true to invert the logic of the endstop.
#define Z_MIN_PROBE_ENDSTOP_INVERTING false // Set to true to invert the logic of the probe.
#define X_DRIVER_TYPE  DRV8825
#define Y_DRIVER_TYPE  DRV8825
#define Z_DRIVER_TYPE  DRV8825
#define E0_DRIVER_TYPE DRV8825
#define DEFAULT_AXIS_STEPS_PER_UNIT   { 200, 200, 3200, 316 }
#define DEFAULT_MAX_FEEDRATE          { 400, 400, 2, 50 }
#define DEFAULT_MAX_ACCELERATION      { 400, 400, 40, 5000 }
#define DEFAULT_ACCELERATION          3000    // X, Y, Z and E acceleration for printing moves
#define DEFAULT_RETRACT_ACCELERATION  3000    // E acceleration for retracts
#define DEFAULT_TRAVEL_ACCELERATION   3000    // X, Y, Z acceleration for travel (non printing) moves
#define DEFAULT_EJERK    5.0  // May be used by Linear Advance
  #define JUNCTION_DEVIATION_MM 0.013 // (mm) Distance from real junction edge
#define S_CURVE_ACCELERATION
#define Z_MIN_PROBE_USES_Z_MIN_ENDSTOP_PIN
#define NOZZLE_TO_PROBE_OFFSET { 10, 10, 0 }
#define MIN_PROBE_EDGE 10
#define XY_PROBE_SPEED 8000
#define Z_PROBE_SPEED_FAST HOMING_FEEDRATE_Z
#define Z_PROBE_SPEED_SLOW (Z_PROBE_SPEED_FAST / 2)
#define Z_CLEARANCE_DEPLOY_PROBE   10 // Z Clearance for Deploy/Stow
#define Z_CLEARANCE_BETWEEN_PROBES  5 // Z Clearance between probe points
#define Z_CLEARANCE_MULTI_PROBE     5 // Z Clearance between multiple probes
#define Z_PROBE_LOW_POINT          -2 // Farthest distance below the trigger-point to go before stopping
#define Z_PROBE_OFFSET_RANGE_MIN -20
#define Z_PROBE_OFFSET_RANGE_MAX 20
#define X_ENABLE_ON 0
#define Y_ENABLE_ON 0
#define Z_ENABLE_ON 0
#define E_ENABLE_ON 0 // For all extruders
#define DISABLE_X false
#define DISABLE_Y false
#define DISABLE_Z false
#define DISABLE_E false             // For all extruders
#define DISABLE_INACTIVE_EXTRUDER   // Keep only the active extruder enabled
#define INVERT_X_DIR false
#define INVERT_Y_DIR false
#define INVERT_Z_DIR true
#define INVERT_E0_DIR false
#define INVERT_E1_DIR false
#define INVERT_E2_DIR false
#define INVERT_E3_DIR false
#define INVERT_E4_DIR false
#define INVERT_E5_DIR false
#define INVERT_E6_DIR false
#define INVERT_E7_DIR false
#define X_HOME_DIR -1
#define Y_HOME_DIR -1
#define Z_HOME_DIR -1
#define X_BED_SIZE 150
#define Y_BED_SIZE 150
#define X_MIN_POS -4.0
#define Y_MIN_POS -20.0
#define Z_MIN_POS 0
#define X_MAX_POS X_BED_SIZE
#define Y_MAX_POS Y_BED_SIZE
#define Z_MAX_POS 150
#define MIN_SOFTWARE_ENDSTOPS
  #define MIN_SOFTWARE_ENDSTOP_X
  #define MIN_SOFTWARE_ENDSTOP_Y
  #define MIN_SOFTWARE_ENDSTOP_Z
#define MAX_SOFTWARE_ENDSTOPS
  #define MAX_SOFTWARE_ENDSTOP_X
  #define MAX_SOFTWARE_ENDSTOP_Y
  #define MAX_SOFTWARE_ENDSTOP_Z
#define LEVEL_BED_CORNERS
  #define LEVEL_CORNERS_INSET_LFRB { 30, 30, 30, 30 } // (mm) Left, Front, Right, Back insets
  #define LEVEL_CORNERS_HEIGHT      0.0   // (mm) Z height of nozzle at leveling points
  #define LEVEL_CORNERS_Z_HOP       4.0   // (mm) Z height of nozzle between leveling points
#define HOMING_FEEDRATE_XY (50*60)
#define HOMING_FEEDRATE_Z  (4*60)
#define VALIDATE_HOMING_ENDSTOPS
#define EEPROM_SETTINGS       // Persistent storage with M500 and M501
#define EEPROM_CHITCHAT       // Give feedback on EEPROM commands. Disable to save PROGMEM.
#define EEPROM_BOOT_SILENT    // Keep M503 quiet and only give errors during first load
#define HOST_KEEPALIVE_FEATURE        // Disable this if your host doesn't like keepalive messages
#define DEFAULT_KEEPALIVE_INTERVAL 2  // Number of seconds between "busy" messages. Set with M113.
#define BUSY_WHILE_HEATING            // Some hosts require "busy" messages even during heating
#define PREHEAT_1_LABEL       "PLA"
#define PREHEAT_1_TEMP_HOTEND 200
#define PREHEAT_1_TEMP_BED      0
#define PREHEAT_1_FAN_SPEED     0 // Value from 0 to 255
#define PREHEAT_2_LABEL       "PETG"
#define PREHEAT_2_TEMP_HOTEND 240
#define PREHEAT_2_TEMP_BED      0
#define PREHEAT_2_FAN_SPEED     0 // Value from 0 to 255
#define PRINTJOB_TIMER_AUTOSTART
#define LCD_LANGUAGE en
#define DISPLAY_CHARSET_HD44780 JAPANESE
#define LCD_INFO_SCREEN_STYLE 0
#define SDSUPPORT
#define INDIVIDUAL_AXIS_HOMING_MENU
#define SOFT_PWM_SCALE 0
#define SERVO_DELAY { 300 }

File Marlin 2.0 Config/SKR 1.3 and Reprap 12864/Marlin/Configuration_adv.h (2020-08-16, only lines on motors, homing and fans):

#define E0_AUTO_FAN_PIN FAN1_PIN
#define E1_AUTO_FAN_PIN -1
#define E2_AUTO_FAN_PIN -1
#define E3_AUTO_FAN_PIN -1
#define E4_AUTO_FAN_PIN -1
#define E5_AUTO_FAN_PIN -1
#define E6_AUTO_FAN_PIN -1
#define E7_AUTO_FAN_PIN -1
#define CHAMBER_AUTO_FAN_PIN -1
#define HOMING_BUMP_MM      { 5, 5, 2 }       // (mm) Backoff from endstops after first bump
#define HOMING_BUMP_DIVISOR { 2, 2, 4 }       // Re-Bump Speed Divisor (Divides the Homing Feedrate)
#define MICROSTEP_MODES { 16, 16, 16, 16, 16, 16 } // [1,2,4,8,16]
#define LIN_ADVANCE
  #define LIN_ADVANCE_K 0.6    // Unit: mm compression per 1mm/s extruder speed
#define ADVANCED_PAUSE_FEATURE
  #define ADVANCED_PAUSE_PURGE_FEEDRATE        3  // (mm/s) Extrude feedrate (after loading). Should be slower than load feedrate.
  #define ADVANCED_PAUSE_PURGE_LENGTH         50  // (mm) Length to extrude after loading.
  #define ADVANCED_PAUSE_RESUME_PRIME          0  // (mm) Extra distance to prime nozzle after returning from park.

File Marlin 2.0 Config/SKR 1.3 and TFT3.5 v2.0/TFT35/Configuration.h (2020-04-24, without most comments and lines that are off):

#define _CONFIGRATION_H_
#define DEFAULT_LCD_MODE SERIAL_TSC
#define STARTUP_KNOB_LED_COLOR 1         // LED_OFF
#define KEEP_KNOB_LED_COLOR_MARLIN_MODE  // Keeps the LED state in Marlin Mode
#define DEFAULT_LCD_BRIGHTNESS      11  // 11: LCD_100_PERCENT - Brightness value from list
#define DEFAULT_LCD_IDLE_BRIGHTNESS 2   // 2: LCD_10_PERCENT - Brightness value from list
#define DEFAULT_LCD_IDLE_TIMER      1   // 1: LCD_DIM_OFF
#define LCD_DIM_CUSTOM_SECONDS      600 // Custom value in seconds. Will be used if
#define ST7920_BKCOLOR BLACK
#define ST7920_FNCOLOR YELLOW
#define DEFAULT_ST7920_FULLSCREEN_MODE 0 // 0: Disabled. RECOMMENDED FOR TFT24
#define BAUDRATE 115200
#define DEFAULT_LANGUAGE ENGLISH
#define SHOW_BTT_BOOTSCREEN
#define BUZZER_FREQUENCY_DURATION_MS 20 // Default 20
#define BUZZER_FREQUENCY_HZ 10000       // Default 10000, 20Hz to 60KHz
#define BUZZER_STOP_LEVEL false
#define TITLE_BACKGROUND_COLOR      BLACK  // Title background color // 0xD928
#define BACKGROUND_COLOR            BLACK  // Background color // 0x0A29
#define FONT_COLOR                  WHITE  // Font foreground color
#define REMINDER_FONT_COLOR         RED    // Reminder font color, such as: "No print attached", "Busy processing", etc.
#define VOLUME_REMINDER_FONT_COLOR  GBLUE  // Volume reminder font color, such as: "Card inserted", "Card removed"
#define TOOL_NUM     1    // set in 1~6
#define EXTRUDER_NUM 1    // set in 1~6
#define FAN_NUM      1    // set in 1~6
#define PREHEAT_BED      {0,       0,        0}
#define PREHEAT_HOTEND   {200,     250,      230}
#define HEAT_MAX_TEMP    {150,    275,       275,       275,       275,       275,       275}    //max temperature can be set
#define HEAT_SIGN_ID     {"B:",   "T0:",     "T1:",     "T2:",     "T3:",     "T4:",     "T5:"}
#define HEAT_DISPLAY_ID  {"Bed",  "T0",      "T1",      "T2",      "T3",      "T4",      "T5"}
#define HEAT_CMD         {"M115", "M104 T0", "M104 T1", "M104 T2", "M104 T3", "M104 T4", "M104 T5" };
#define HEAT_WAIT_CMD    {"M115", "M109 T0", "M109 T1", "M109 T2", "M109 T3", "M109 T4", "M109 T5" };
#define TOOL_CHANGE      {"T0",   "T1",      "T2",      "T3",      "T4",      "T5"}
#define EXTRUDER_ID      {"E0",   "E1",      "E2",      "E3",      "E4",      "E5"}
#define FAN_MAX_PWM      {255,       255,       255,       255,       255,       255}
#define FAN_ID           {"F0",    "F1",    "F2",    "F3",    "F4",    "F5"}
#define FAN_CMD          {"M106 P0", "M106 P1", "M106 P2", "M106 P3", "M106 P4", "M106 P5" };
#define SPEED_ID         {"Sp.", "Fr."}
#define AXIS_DISPLAY_ID  {"X",  "Y",  "Z",   "E",  "E2"}
#define DEFAULT_SPEED_MOVE      3000
#define SPEED_MOVE_SLOW         1000
#define SPEED_MOVE_FAST         5000
#define EXTRUDE_SLOW_SPEED      60
#define EXTRUDE_NORMAL_SPEED    600
#define EXTRUDE_FAST_SPEED      1200
#define X_MIN_POS 0
#define Y_MIN_POS 0
#define Z_MIN_POS 0
#define X_MAX_POS 150
#define Y_MAX_POS 150
#define Z_MAX_POS 150
#define NOZZLE_PAUSE_RETRACT_LENGTH 15   // (mm)
#define NOZZLE_RESUME_PURGE_LENGTH  16   // (mm)
#define NOZZLE_PAUSE_X_POSITION     (X_MIN_POS + 10)  // (mm) Must be an integer
#define NOZZLE_PAUSE_Y_POSITION     (Y_MIN_POS + 10)  // (mm) Must be an integer
#define NOZZLE_PAUSE_Z_RAISE        20   // (mm)
#define NOZZLE_PAUSE_E_FEEDRATE     6000 // (mm/min) retract & purge feedrate
#define NOZZLE_PAUSE_XY_FEEDRATE    6000 // (mm/min) X and Y axes feedrate
#define NOZZLE_PAUSE_Z_FEEDRATE     600  // (mm/min) Z axis feedrate
#define AUTO_SAVE_LOAD_LEVELING_VALUE
#define LEVELING_POINT_1_X         (X_MIN_POS + 30)
#define LEVELING_POINT_1_Y         (Y_MIN_POS + 30)
#define LEVELING_POINT_2_X         (X_MAX_POS - 30)
#define LEVELING_POINT_2_Y         (Y_MIN_POS + 30)
#define LEVELING_POINT_3_X         (X_MAX_POS - 30)
#define LEVELING_POINT_3_Y         (Y_MAX_POS - 30)
#define LEVELING_POINT_4_X         (X_MIN_POS + 30)
#define LEVELING_POINT_4_Y         (Y_MAX_POS - 30)
#define LEVELING_POINT_Z           0.2f  // Z-axis position when nozzle stays for leveling
#define LEVELING_POINT_MOVE_Z      10.0f // Z-axis position when nozzle move to next point
#define LEVELING_POINT_XY_FEEDRATE 6000  // (mm/min) X and Y axes move feedrate
#define LEVELING_POINT_Z_FEEDRATE  600   // (mm/min) Z axis move feedrate
#define PS_ON_ACTIVE_HIGH    true   // Set 'false' for ATX (1), 'true' for X-Box (2)
#define FIL_RUNOUT_INVERTING true  // Set to false to invert the logic of the sensor.
#define FIL_NOISE_THRESHOLD  100   // 100ms,  Pause print when filament runout is detected for 100ms.
#define FILAMENT_RUNOUT_DISTANCE_MM 7
#define ALTERNATIVE_MOVE_MENU
#define UNIFIED_MENU
#define ONBOARD_SD_SUPPORT
  #define M27_REFRESH                3        // Time in sec for M27 command
  #define M27_WATCH_OTHER_SOURCES    true     // if true the polling on M27 report is always active. Case: SD print started not from TFT35
#define POWER_LOSS_ZRAISE 10 // (mm) Raise Z axis on resume (on power loss with UPS)
#define PREVENT_COLD_EXTRUSION_MINTEMP 180
#define AUTO_SHUT_DOWN_MAXTEMP 50
#define SHOW_FAN_PERCENTAGE // enable to show fan speed as a percentage instead of a value
#define RAPID_SERIAL_COMM
#define CUSTOM_0_LABEL "Disable Steppers"
#define CUSTOM_0_GCODE "M84\n"
#define CUSTOM_1_LABEL "Init SD Card"
#define CUSTOM_1_GCODE "M21\n"
#define CUSTOM_2_LABEL "Release SD Card"
#define CUSTOM_2_GCODE "M22\n"
#define CUSTOM_3_LABEL "Enable Leveling State"
#define CUSTOM_3_GCODE "M420 S1\n"
#define CUSTOM_4_LABEL "Save to EEPROM"
#define CUSTOM_4_GCODE "M500\n"
#define CUSTOM_5_LABEL "Restore from EEPROM"
#define CUSTOM_5_GCODE "M501\n"
#define CUSTOM_6_LABEL "EEPROM Defaults"
#define CUSTOM_6_GCODE "M502\n"
#define PRINT_START_GCODE "G28 XY R10\n" // Raise Z 10mm before homing X & Y
#define PRINT_END_GCODE "G90\nG1 E-4\nG92 E0\nM18\n" // Switch to absolute positioning, reduce filament pressure by performing small retract, reset extruder position, disable steppers
#define PRINT_CANCEL_GCODE "G28 XY R10\n" // Home XY and raise Z 10mm

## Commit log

2019-10-14 Add Windows driver for USB interface
2019-10-14 Add factory documentation and test model
    [20mm_box_pillar.stl]
2019-10-14 Add my print and filament settings
2019-10-14 add calibration cube
    [xyzCalibration_cube.stl]
2019-10-14 add z axis stabilizer
    [Tronxy-X1_Z_Axis_Rod_Stabilizer.fcstd, tronxy-x1-z-axis-stabilizer.stl]
2019-10-14 Add part cooling fan shroud
    [fanshrout.stl]
2019-10-19 add note about painter's tape for the bed
2019-10-19 add snappy slop calibrator model
    [slop_calibrator_parts.stl]
2019-10-19 increase travel speed, increase retraction distance to combat stringing. decrease first layer height to help gear bearing model gear freeze
2019-10-19 add petsfang cooler and spare brackets set
    [E3DV6_TRONXY_BLT_X5_ENDSTOP_V6.28_TAREK.stl, E3DV6_TRONXY_X5_OR_X1_MANUAL_BASE_V8.8.stl, E3DV6_Tronxy_STOCKFAN_CAP_V6.28.stl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]
2019-10-20 add benchy and stringing test
    [3DBenchy.3mf, 3DBenchy_-_Multi-part_-_Single_-_Bridge_roof_-_3DBenchy.com.stl, 3DBenchy_-_Multi-part_-_Single_-_Bridge_walls_-_3DBenchy.com.stl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]
2019-10-20 reduce temperature to combat stringing
2019-10-20 set nozzle size implicitly, increase retraction and disable zhop to combat stringing, enlarge skirt and brim for adhesion on small parts
2019-10-20 add control box model
    [X1_Control_Box_and_base-V2-BASE-CENTER.stl, X1_Control_Box_and_base-V2-BASE-LEFT-.stl, X1_Control_Box_and_base-V2-BASE-RIGHT.stl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]
2019-10-20 add button caps
    [caps.stl]
2019-10-26 bump temperature to 220
2019-11-02 move petsfang to proper directory, add belt tensioner that does not require additional hardware
    [Belt_tensioner.stl, Belt_tensioner_-_Bracket.stl, Belt_tensioner_-_EndCap.stl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]
2019-11-04 add first layer calibration
    [First_layer_calibration.stl]
2019-11-05 more profile tuning and add 0.3mm layer settings
2019-11-13 add calibration stick
    [calibration_axis.STL]
2019-11-17 add/reorg models
    [0.1.stl, 0.15.stl, 0.2.stl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]
2019-12-25 Update README, add marlin 2.0 config files
    [Configuration.h, Configuration_adv.h]
2019-12-25 set flow back to 100
2019-12-27 add customizable spool adapter
    [spool_adapter_V1.4.scad]
2019-12-28 correct extruder steps/mm
    [Configuration.h]
2019-12-28 sync config changes from 2.0.1
    [Configuration.h]
2019-12-28 sync changes from 2.0.1
    [Configuration_adv.h]
2019-12-29 update for loss of bed area due to tensioner
    [Configuration.h]
2019-12-29 update bed size
    [Configuration.h]
2020-01-04 update pid
    [Configuration.h]
2020-01-06 add new bracket design
    [bracket.scad, bracket.stl]
2020-01-06 add triangular cutout to reduce material
    [bracket.scad, bracket.stl]
2020-01-06 tweak model dimensions
    [bracket.scad, bracket.stl]
2020-01-09 set bed back to 150x150
    [Configuration.h]
2020-02-09 add z motor mount
    [TronXY_Z-AXIS_MOTOR_MOUNT.stl]
2020-02-10 update extruder steps/mm for leoway extruder https://www.amazon.ca/gp/product/B07XKKX2FY/ref=ppx_yo_dt_b_search_asin_title?ie=UTF8&psc=1
    [Configuration.h]
2020-02-10 extruder steps per m for PLA w leoway extruder
    [Configuration.h]
2020-04-02 update max hotend temp to 300 and set thermistor value for https://www.aliexpress.com/item/32920338250.html "HT-NTC100K, B3950"
    [Configuration.h]
2020-04-02 Update config to support Marlin 2.0.5.3
    [Configuration.h, Configuration_adv.h]
2020-04-02 update for TriangleLab ATC Semitec 104GT-2 https://www.aliexpress.com/item/32844028127.html
    [Configuration.h]
2020-04-03 update config
    [Configuration.h]
2020-04-04 add config for SKR 1.3 and TFT35 2.0 for Tronxy X1
    [Configuration.h, Configuration_adv.h]
2020-04-04 adjust bed offset
    [Configuration.h]
2020-04-08 set sane default for linear advance and tune esteps
    [Configuration.h, Configuration_adv.h]
2020-04-14 add a temp tower, update petg profile
    [tempTower.scad, tempTower.stl]
2020-04-24 update config files and pla profile
    [Configuration.h]
2020-04-24 enable power loss recovery by default
    [Configuration_adv.h]
2020-04-24 work around https://github.com/bigtreetech/BIGTREETECH-TouchScreenFirmware/issues/571
    [Configuration.h]
2020-05-27 fix esteps and encoder direction
    [Configuration.h]
2020-05-31 new test cube
    [super_cube.scad, super_cube.stl]
2020-05-31 add new improved z axis stabilizer
    [Tronxy-X1_Z_Axis_Rod_Stabilizer.fcstd, Z-Axis Stabilizer v14.f3d, Z-Axis Stabilizer v14.stl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]
2020-06-02 add filament change, adjust z feedrate, fix encoder direction
    [Configuration.h, Configuration_adv.h]
2020-06-24 adjust dimensions
    [Configuration.h]
2020-08-16 update for tmc2208 on x/y
    [Configuration.h]
2020-08-16 port config to marlin 2.0.6
    [Configuration.h, Configuration_adv.h]

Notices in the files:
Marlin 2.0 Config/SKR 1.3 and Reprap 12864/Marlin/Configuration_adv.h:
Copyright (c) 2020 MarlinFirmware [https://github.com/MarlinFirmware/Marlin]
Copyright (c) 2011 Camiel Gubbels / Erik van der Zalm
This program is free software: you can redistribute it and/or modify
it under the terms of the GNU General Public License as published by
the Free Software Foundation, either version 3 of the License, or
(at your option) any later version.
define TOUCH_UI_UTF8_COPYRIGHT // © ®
